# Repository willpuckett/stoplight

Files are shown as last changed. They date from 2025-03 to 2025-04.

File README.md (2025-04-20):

# 🚥 Stoplight

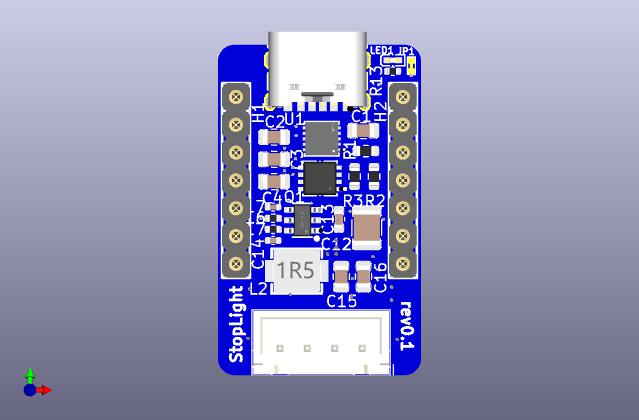
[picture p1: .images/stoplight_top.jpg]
top_view


### Features

- TMC2209 Stepper Driver
- 1 Ω Sense Resistors (tuned for small motors)
- HUSB238 PD Controller for dynamic Voltage Control
- On-board temperature sensing

Stoplight is a Xiao shield for operating small stepper motors. It is designed
specifically for 28-BYJ48, although it _may_ work with other small (0.225 RMS Amps or less) steppers as
well. It aims to provide utility all around the home, and is especially useful
when working with blinds and knobs.

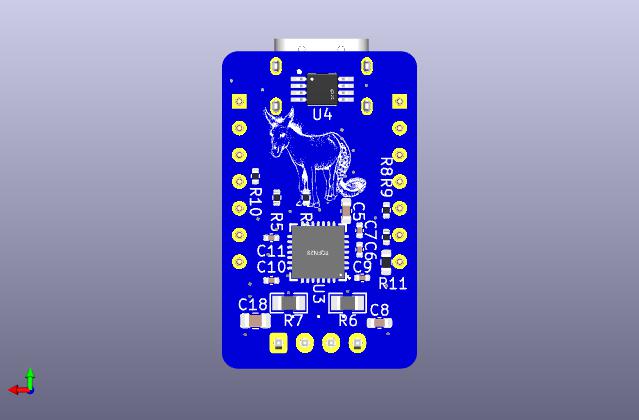
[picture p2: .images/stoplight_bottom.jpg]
rear pcb view


Commercial stepsticks have sense resistors that are not properly sized for
'smaller' motors to take advantage of TMC2209's features, including
stallguard.

> StopLight brings stall sensing to commodity/low cost, high torque motors.

Stoplight seeks to remedy these issues, while also providing software selectable
voltage control and temperature measurement in a package that works well with
HomeAssistant/ESPHome.

### Todo 

- [ ] TVS Protection
- [ ] Change C14 to same as C18 (BOM Consolidation)
- [ ] Consider removing DIAG and just using UART events instead
- [ ] Consider reconneacting fan port
- [ ] Address DS18B20U reading high 
- [ ] Test fit in mini blind housing
- [ ] Dim LED brightness
- [x] Test StallGuard tuning
  - ✅ works very well at 12v+
  - ⚠️ 9v is untested 
  - 🚦 5v is more finicky
- [x] Add esphome sample yaml's

## Homing

homing demo

## Fabrication

Use the [production files](jlcpcb/production_files/) to upload to jlc. Or first run [available here](https://octule.com/listing/1891073906/stoplight).

You'll need to swap the motor wires to a JST XH 4 pin housing. In addition to
removing the red cable, you also **must** perform the
[bipolar mod](https://ardufocus.com/howto/28byj-48-bipolar-hw-mod/) on your
steppers.

## Example HomeAssistant Config

The build sometimes fails, but can usually be completed by repeatedly pressing
'Retry', or switching to 'arduino' framework.

### Tuning

<details><summary>This demo exposes a number of controls to make tuning StallGuard easier.</summary>

```yaml
substitutions:
  name: "stoplight"
  friendly_name: "StopLight"
  board: "seeed_xiao_esp32c3"

# board/wifi/ota stuff
packages:
  device_base: !include .esp32.yaml

esp32:
  framework:
    type: esp-idf

logger:
  level: DEBUG

esphome:
  on_boot:
    - tmc2209.configure:
        direction: cw # or ccw
        microsteps: 1
        interpolation: True
        enable_spreadcycle: False
        tcool_threshold: 0
        tpwm_threshold: 0
    - tmc2209.stallguard:
        threshold: 23
    - tmc2209.currents:
        standstill_mode: freewheeling
        run_current: 0.150 # was 0.240
        hold_current: 0
    - button.press: home # home right after boot

external_components:
  - source: github://slimcdk/esphome-custom-components
    components: [tmc2209_hub, tmc2209, stepper]
  - source: github://pr#6693
    components: [husb238]

globals:
  - id: has_homed
    type: bool
    initial_value: "true"
    restore_value: no
  - id: homing_speed
    type: int
    initial_value: "480"
    restore_value: True

web_server:
  port: 80

i2c:
  sda: GPIO6
  scl: GPIO7
  frequency: 800kHz

uart:
  tx_pin: GPIO21
  rx_pin: GPIO20
  baud_rate: 500000 # 9600 -> 500k

one_wire:
  - platform: gpio
    pin: GPIO10

stepper:
  - platform: tmc2209
    id: driver
    # https://www.klipper3d.org/TMC_Drivers.html#limitations
    max_speed: 2000 steps/s # was 4000
    acceleration: 1000 steps/s^2 # was 2500
    deceleration: 1000 steps/s^2 # was 2500
    index_pin: GPIO3
    diag_pin: GPIO4
    rsense: 1000 mOhm
    config_dump_include_registers: False
    vsense: False
    analog_current_scale: False
    on_stall:
      - logger.log: "Motor stalled!"
      - if:
          condition:
            lambda: return !id(has_homed);
          then:
            - stepper.stop: driver
            - tmc2209.configure:
                direction: cw # or ccw
                microsteps: 1
                interpolation: True
                enable_spreadcycle: False
                tcool_threshold: 0
            - stepper.report_position:
                id: driver
                position: 0
            - globals.set:
                id: has_homed
                value: "true"
            - logger.log: "Home position set"
            - tmc2209.disable
    on_status:
      - logger.log:
          format: "Driver is reporting an update! (code %d)"
          args: ["code"]
      - if:
          condition:
            lambda: return code == tmc2209::DIAG_TRIGGERED;
          then:
            - logger.log: DIAG_TRIGGERED
      - if:
          condition:
            lambda: return code == tmc2209::DIAG_TRIGGER_CLEARED;
          then:
            - logger.log: DIAG_TRIGGER_CLEARED
      - if:
          condition:
            lambda: return code == tmc2209::RESET;
          then:
            - logger.log: RESET
      - if:
          condition:
            lambda: return code == tmc2209::RESET_CLEARED;
          then:
            - logger.log: RESET_CLEARED
      - if:
          condition:
            lambda: return code == tmc2209::DRIVER_ERROR;
          then:
            - logger.log: DRIVER_ERROR
      - if:
          condition:
            lambda: return code == tmc2209::DRIVER_ERROR_CLEARED;
          then:
            - logger.log: DRIVER_ERROR_CLEARED
      - if:
          condition:
            lambda: return code == tmc2209::CP_UNDERVOLTAGE;
          then:
            - logger.log: CP_UNDERVOLTAGE
      - if:
          condition:
            lambda: return code == tmc2209::CP_UNDERVOLTAGE_CLEARED;
          then:
            - logger.log: CP_UNDERVOLTAGE_CLEARED
      - if:
          condition:
            lambda: return code == tmc2209::OVERTEMPERATURE_PREWARNING;
          then:
            - logger.log: OVERTEMPERATURE_PREWARNING
      - if:
          condition:
            lambda: return code == tmc2209::OVERTEMPERATURE_PREWARNING_CLEARED;
          then:
            - logger.log: OVERTEMPERATURE_PREWARNING_CLEARED
      - if:
          condition:
            lambda: return code == tmc2209::OVERTEMPERATURE;
          then:
            - logger.log: OVERTEMPERATURE
      - if:
          condition:
            lambda: return code == tmc2209::OVERTEMPERATURE_CLEARED;
          then:
            - logger.log: OVERTEMPERATURE_CLEARED
      - if:
          condition:
            lambda: return code == tmc2209::TEMPERATURE_ABOVE_120C;
          then:
            - logger.log: TEMPERATURE_ABOVE_120C
      - if:
          condition:
            lambda: return code == tmc2209::TEMPERATURE_BELOW_120C;
          then:
            - logger.log: TEMPERATURE_BELOW_120C
      - if:
          condition:
            lambda: return code == tmc2209::TEMPERATURE_ABOVE_143C;
          then:
            - logger.log: TEMPERATURE_ABOVE_143C
      - if:
          condition:
            lambda: return code == tmc2209::TEMPERATURE_BELOW_143C;
          then:
            - logger.log: TEMPERATURE_BELOW_143C
      - if:
          condition:
            lambda: return code == tmc2209::TEMPERATURE_ABOVE_150C;
          then:
            - logger.log: TEMPERATURE_ABOVE_150C
      - if:
          condition:
            lambda: return code == tmc2209::TEMPERATURE_BELOW_150C;
          then:
            - logger.log: TEMPERATURE_BELOW_150C
      - if:
          condition:
            lambda: return code == tmc2209::TEMPERATURE_ABOVE_157C;
          then:
            - logger.log: TEMPERATURE_ABOVE_157C
      - if:
          condition:
            lambda: return code == tmc2209::TEMPERATURE_BELOW_157C;
          then:
            - logger.log: TEMPERATURE_BELOW_157C
      - if:
          condition:
            lambda: return code == tmc2209::OPEN_LOAD;
          then:
            - logger.log: OPEN_LOAD
      - if:
          condition:
            lambda: return code == tmc2209::OPEN_LOAD_CLEARED;
          then:
            - logger.log: OPEN_LOAD_CLEARED
      - if:
          condition:
            lambda: return code == tmc2209::OPEN_LOAD_A;
          then:
            - logger.log: OPEN_LOAD_A
      - if:
          condition:
            lambda: return code == tmc2209::OPEN_LOAD_A_CLEARED;
          then:
            - logger.log: OPEN_LOAD_A_CLEARED
      - if:
          condition:
            lambda: return code == tmc2209::OPEN_LOAD_B;
          then:
            - logger.log: OPEN_LOAD_B
      - if:
          condition:
            lambda: return code == tmc2209::OPEN_LOAD_B_CLEARED;
          then:
            - logger.log: OPEN_LOAD_B_CLEARED
      - if:
          condition:
            lambda: return code == tmc2209::LOW_SIDE_SHORT;
          then:
            - logger.log: LOW_SIDE_SHORT
      - if:
          condition:
            lambda: return code == tmc2209::LOW_SIDE_SHORT_CLEARED;
          then:
            - logger.log: LOW_SIDE_SHORT_CLEARED
      - if:
          condition:
            lambda: return code == tmc2209::LOW_SIDE_SHORT_A;
          then:
            - logger.log: LOW_SIDE_SHORT_A
      - if:
          condition:
            lambda: return code == tmc2209::LOW_SIDE_SHORT_A_CLEARED;
          then:
            - logger.log: LOW_SIDE_SHORT_A_CLEARED
      - if:
          condition:
            lambda: return code == tmc2209::LOW_SIDE_SHORT_B;
          then:
            - logger.log: LOW_SIDE_SHORT_B
      - if:
          condition:
            lambda: return code == tmc2209::LOW_SIDE_SHORT_B_CLEARED;
          then:
            - logger.log: LOW_SIDE_SHORT_B_CLEARED
      - if:
          condition:
            lambda: return code == tmc2209::GROUND_SHORT;
          then:
            - logger.log: GROUND_SHORT
      - if:
          condition:
            lambda: return code == tmc2209::GROUND_SHORT_CLEARED;
          then:
            - logger.log: GROUND_SHORT_CLEARED
      - if:
          condition:
            lambda: return code == tmc2209::GROUND_SHORT_A;
          then:
            - logger.log: GROUND_SHORT_A
      - if:
          condition:
            lambda: return code == tmc2209::GROUND_SHORT_A_CLEARED;
          then:
            - logger.log: GROUND_SHORT_A_CLEARED
      - if:
          condition:
            lambda: return code == tmc2209::GROUND_SHORT_B;
          then:
            - logger.log: GROUND_SHORT_B
      - if:
          condition:
            lambda: return code == tmc2209::GROUND_SHORT_B_CLEARED;
          then:
            - logger.log: GROUND_SHORT_B_CLEARED

button:
  - platform: template
    name: Home
    id: home
    on_press:
      - logger.log: "Going home!"
      - tmc2209.configure:
          direction: cw # or ccw
          microsteps: 1
          interpolation: True
          enable_spreadcycle: False
          tcool_threshold: 104
          tpwm_threshold: 0
      # - lambda: id(driver)->write_register(TPWMTHRS, 0);
      # - lambda: id(driver)->write_register(TCOOLTHRS, 1048575);
      - globals.set:
          id: has_homed
          value: "false"
      - stepper.set_speed:
          id: driver
          # 60 to 300 rpm
          speed: !lambda return id(homing_speed);
      - stepper.set_target:
          id: driver
          target: -9999999
  - platform: template
    name: Stop
    id: stop
    on_press:
      - logger.log: "Stopping!"
      - stepper.stop: driver
      - tmc2209.disable
  - platform: template
    name: 1000 Steps forward
    on_press:
      - logger.log: "Going forward!"
      - stepper.set_speed:
          id: driver
          speed: 400 steps/s
      - stepper.set_target:
          id: driver
          target: !lambda return id(driver)->current_position +1000;
      # - tmc2209.disable

husb238:
  id: husb_01

binary_sensor:
  - platform: husb238
    attached: "PD Attached"

  - platform: template
    name: "Has Homed"
    lambda: return id(has_homed);

text_sensor:
  - platform: husb238
    status: "Last request status"
    capabilities: "Capabilities"

select:
  - platform: husb238
    voltage: "Voltage selector"

sensor:
  - platform: husb238
    voltage: "Contracted Voltage"
    current: "Contracted Current"
    selected_voltage: "Selected Voltage"

  - platform: dallas_temp
    name: temperature

  - platform: tmc2209
    type: stallguard_result
    name: Driver stallguard
    update_interval: 10s

  - platform: tmc2209
    type: actual_current
    name: Actual current
    update_interval: 10s

  - platform: tmc2209
    type: motor_load
    name: Motor load
    update_interval: 10s

  # - platform: tmc2209
  #   type: pwm_scale_sum
  #   name: PWM Scale Sum
  #   update_interval: 250ms

  # - platform: tmc2209
  #   type: pwm_scale_auto
  #   name: PWM Scale Auto
  #   update_interval: 250ms

  # - platform: tmc2209
  #   type: pwm_ofs_auto
  #   name: PWM OFS Auto
  #   update_interval: 250ms

  # - platform: tmc2209
  #   type: pwm_grad_auto
  #   name: PWM Grad Auto
  #   update_interval: 250ms

number:
  - platform: template
    name: Target position
    min_value: -999999
    max_value: 999999
    step: 100
    lambda: return id(driver)->current_position;
    update_interval: 10s
    set_action:
      - stepper.set_target:
          id: driver
          target: !lambda "return x;"

  - platform: template
    name: Homing RPM
    min_value: 0
    max_value: 300
    step: 1
    lambda: return id(homing_speed) * 60 / 32;
    update_interval: 10s
    set_action:
      - globals.set:
          id: homing_speed
          value: !lambda "return x * 32 / 60;"

  - platform: template
    name: SGTHRS
    min_value: 0
    max_value: 255
    step: 1
    lambda: return id(driver)->read_register(SGTHRS);
    update_interval: 10s
    set_action:
      - lambda: id(driver)->write_register(SGTHRS, x);

  - platform: template
    name: TCOOLTHRS
    min_value: 0
    max_value: 1048575
    step: 1
    lambda: return id(driver)->read_register(TCOOLTHRS);
    update_interval: 10s
    set_action:
      - lambda: id(driver)->write_register(TCOOLTHRS, x);

  - platform: template
    name: "Run Current"
    min_value: 0
    max_value: 31
    step: 1
    lambda: return id(driver)->read_field(IRUN_FIELD);
    update_interval: 10s
    set_action:
      - tmc2209.currents:
          irun: !lambda "return x;"
```
</details>

### Wall Heater

<details><summary>This demo implements a knob controlled wall heater.</summary>

```yaml
substitutions:
  name: "heater"
  friendly_name: "Wall Heater"
  board: "seeed_xiao_esp32c3"

# board/wifi/ota stuff
packages:
  device_base: !include .esp32.yaml

esphome:
  on_boot:
    # - lambda: id(husb_01)->command_request_voltage(5);
    - tmc2209.configure:
        direction: cw # or ccw
        microsteps: 1
        interpolation: True
        enable_spreadcycle: False
        tcool_threshold: 0
        tpwm_threshold: 0
    - tmc2209.stallguard:
        threshold: 23
    - tmc2209.currents:
        standstill_mode: freewheeling
        run_current: 0.1375 # was 0.150
        hold_current: 0
    - button.press: probe_low # home right after boot

external_components:
  - source: github://slimcdk/esphome-custom-components
    components: [ tmc2209_hub, tmc2209, stepper ]
  - source: github://pr#6693
    components: [ husb238 ]

globals:
  - id: steps
    type: int
    restore_value: yes
    initial_value: "1000"

i2c:
  sda: GPIO6
  scl: GPIO7 
  frequency: 800kHz

uart:
  tx_pin: GPIO21
  rx_pin: GPIO20
  baud_rate: 500000 # 9600 -> 500k

one_wire:
  - platform: gpio
    pin: GPIO10

husb238:
  id: husb_01

stepper:
  - platform: tmc2209
    id: driver
    max_speed: 480 steps/s
    acceleration: 1000 steps/s^2 
    deceleration: 1000 steps/s^2 
    index_pin: GPIO3
    diag_pin: GPIO4
    rsense: 1000 mOhm
    on_stall:
      - stepper.stop: driver
      - logger.log: Endstop Detected 🍍

script:
  - id: move_stepper
    mode: restart
    parameters:
      # use 0/false for low side endstop, 1/true for high side
      homing: bool
      target: int
    then:
      - lambda: id(husb_01)->command_request_voltage(20);
      - tmc2209.configure:
          tcool_threshold: !lambda 'return homing ? 104 : 0;'
      - stepper.set_speed:
          id: driver
          speed: 480 steps/s
      - delay: 1s
      - stepper.set_target:
          id: driver
          target: !lambda 'return target;'
      - wait_until:
          condition:
            lambda: 'return id(driver)->has_reached_target();'
      - logger.log:
          format: "Moved to %d steps"
          args: [ 'id(driver)->current_position' ]
      - tmc2209.disable:
          id: driver 
      - lambda: id(husb_01)->command_request_voltage(5);

button:
  - platform: template
    name: Probe Low
    id: probe_low 
    on_press:
      - climate.control:
          id: pid_climate
          mode: 'OFF'
      - script.execute: 
          id: move_stepper
          homing: true
          target: -9999999
      - script.wait: move_stepper
      - stepper.report_position:
          id: driver
          position: 0
      - logger.log:
          format: "Probed to %d steps"
          args: [ 'id(driver)->current_position' ]
      
  - platform: template
    name: Probe High
    id: probe_high
    on_press:
      - climate.control:
          id: pid_climate
          mode: 'OFF'
      - script.execute: 
          id: move_stepper
          homing: true
          target: 9999999
      - script.wait: move_stepper
      - globals.set:
          id: steps
          value: !lambda 'return id(driver)->current_position;'
 
  - platform: template
    name: "PID Climate Autotune"
    on_press:
      - climate.pid.autotune: pid_climate

sensor:
  - platform: husb238
    voltage: "Contracted Voltage"

  - platform: template
    name: "Steps"
    id: steps_display
    icon: "mdi:shoe-print"
    accuracy_decimals: 0
    lambda: 'return id(steps);'

  - platform: dallas_temp
    id: ds_temp
    filters: 
      - lambda: return x - 13.5;

  # This sensor takes the output from the pid heater and transforms it to step numbers
  - platform: pid
    name: "PID Climate Heat"
    id: heat_float
    type: HEAT
    filters:
      - round_to_multiple_of: 10
      - delta: 9
    on_value:
      then:
        - script.execute: 
            id: move_stepper
            homing: false
            target: !lambda 'return static_cast<int>(id(steps) * (x / 100));'

# This is just a fake output to make the pid heater happy.
# Ideally, the pin will use the onboard led, but I'm not sure what the pin number is for that...
output:
  - platform: ledc
    pin: GPIO2
    id: heater_output

# Example configuration entry
climate:
  - platform: pid
    name: "PID Climate Controller"
    id: pid_climate
    sensor: ds_temp
    default_target_temperature: 21°C
    heat_output: heater_output
    control_parameters:
      kp: 4
      ki: 0.4
      kd: 0.5
      output_averaging_samples: 5      # smooth the output over 5 samples
      derivative_averaging_samples: 5  # smooth the derivative value over 5 samples
    # deadband_parameters:
    #   threshold_high: 0.5°C
    #   threshold_low: -1.0°C
    #   kp_multiplier: 0.5   # proportional gain reduced inside deadband
    #   ki_multiplier: 0.25   # integral accumulates at only 25% of normal ki
    #   kd_multiplier: 0.5   # derviative is reduced inside deadband
    #   deadband_output_averaging_samples: 5   # average the output over 15 samples within the deadband
```

</details>

### Blinds

<details><summary>StallGuard blinds operation</summary>

```yaml
substitutions:
  name: "blins03"
  blind_number: right
  friendly_name: "Right Blind"
  board: "seeed_xiao_esp32c3"
  delay: "1s"

# board/wifi/ota stuff
packages:
  device_base: !include .esp32.yaml

esphome:
  on_boot:
    - tmc2209.configure:
        direction: ccw # or ccw
        microsteps: 1
        interpolation: True
        enable_spreadcycle: False
        tcool_threshold: 0
        tpwm_threshold: 0
    - tmc2209.stallguard:
        threshold: 45 
    - tmc2209.currents:
        standstill_mode: freewheeling
        run_current: 0.1375 # was 0.150
        hold_current: 0

external_components:
  - source: github://slimcdk/esphome-custom-components
    components: [ tmc2209_hub, tmc2209, stepper ]
  - source: github://pr#6693
    components: [ husb238 ]

globals:
  - id: steps
    type: int
    restore_value: yes
    initial_value: "1000"

i2c:
  sda: GPIO6
  scl: GPIO7 
  frequency: 800kHz

uart:
  tx_pin: GPIO21
  rx_pin: GPIO20
  baud_rate: 500000 # 9600 -> 500k

one_wire:
  - platform: gpio
    pin: GPIO10

husb238:
  id: husb_01

stepper:
  - platform: tmc2209
    id: driver
    max_speed: 480 steps/s
    acceleration: 1000 steps/s^2 
    deceleration: 1000 steps/s^2 
    index_pin: GPIO3
    diag_pin: GPIO4
    rsense: 1000 mOhm
    on_stall:
      - stepper.stop: driver
      - logger.log: Endstop Detected 🍍

script:
  - id: move_stepper
    mode: restart
    parameters:
      # use 0/false for low side endstop, 1/true for high side
      homing: bool
      target: int
    then:
      - lambda: id(husb_01)->command_request_voltage(12);
      - tmc2209.configure:
          tcool_threshold: !lambda 'return homing ? 104 : 0;'
      - stepper.set_speed:
          id: driver
          speed: !lambda 'return homing ? 480 : 120;'
      - delay: 1s
      - stepper.set_target:
          id: driver
          target: !lambda 'return target;'
      - while:
          condition:
            lambda: 'return !id(driver)->has_reached_target();'
          then:
            - cover.template.publish:
                id: ${name}_${blind_number}
                position: !lambda 'return float( id(driver).current_position ) / float( id(steps) );' 
                current_operation: !lambda 'return id(driver).current_position < id(driver).target_position ? COVER_OPERATION_OPENING : COVER_OPERATION_CLOSING;'
            - delay: ${delay}
      - logger.log:
          format: "Moved to %d steps"
          args: [ 'id(driver)->current_position' ]
      - tmc2209.disable:
          id: driver 
      - lambda: id(husb_01)->command_request_voltage(5);
      - cover.template.publish:
          id: ${name}_${blind_number}
          position: !lambda 'return float( id(driver).current_position ) / float( id(steps) );' 
          current_operation: IDLE

button:
  - platform: template
    name: Probe Low
    id: probe_low 
    on_press:
      - script.execute: 
          id: move_stepper
          homing: true
          target: -9999999
      - script.wait: move_stepper
      - stepper.report_position:
          id: driver
          position: 0
      - logger.log:
          format: "Probed to %d steps"
          args: [ 'id(driver)->current_position' ]
      
  - platform: template
    name: Probe High
    id: probe_high
    on_press:
      - script.execute: 
          id: move_stepper
          homing: true
          target: 9999999
      - script.wait: move_stepper
      - globals.set:
          id: steps
          value: !lambda 'return id(driver)->current_position;'

sensor:
  - platform: husb238
    voltage: "Contracted Voltage"

  - platform: template
    name: "Steps"
    id: steps_display
    icon: "mdi:shoe-print"
    accuracy_decimals: 0
    lambda: 'return id(steps);'

  - platform: dallas_temp
    id: ds_temp
    filters: 
      - lambda: return x - 13.5;

cover:
  - platform: template
    name: "${blind_number}"
    id: ${name}_${blind_number}
    open_action:
      then:
        - logger.log: "Opening"
        - button.press: probe_high
    close_action:
      then:
        - logger.log: "Closing"
        - button.press: probe_low
    position_action:
      then:
        - logger.log: "Jostling"
        - script.execute: 
            id: move_stepper
            homing: false
            target: !lambda return int(id(steps) * pos);
    stop_action:
      then:
        - script.execute: 
            id: move_stepper
            homing: false
            target: !lambda return id(driver).current_position;
    has_position: true
    device_class: blind

switch:
  - platform: template
    name: "Reset ${blind_number}"
    id: reset_${name}_${blind_number}
    turn_on_action:
      - button.press: probe_low
      - script.wait: move_stepper
      - button.press: probe_high
      - script.wait: move_stepper
      - button.press: probe_low
      - script.wait: move_stepper
      - switch.turn_off: reset_${name}_${blind_number}
```

</details>

## Schematic

schematic

## Reference

[TMC2209 Calaulations Worksheet](https://www.analog.com/media/en/engineering-tools/design-tools/TMC2209_Calculations.xlsx)

[BTT-TMC2209-v1.2](https://pax.deno.dev/bigtreetech/BIGTREETECH-TMC2209-V1.2@master/Schematic/TMC2209-V1.2.pdf?b)

[Cookie Robotics](https://cookierobotics.com/042/)

[jangeox](http://www.jangeox.be/2013/10/change-unipolar-28byj-48-to-bipolar.html)

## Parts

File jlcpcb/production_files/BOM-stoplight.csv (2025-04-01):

Comment | Designator | Footprint | LCSC | Quantity
4K7 | R12 | R_0402_1005Metric | C105871 | 1
56pF | C8 | C_0402_1005Metric | C107007 | 1
10R | R1 | R_0603_1608Metric | C109318 | 1
2K2 | R10,R11 | R_0402_1005Metric | C114762 | 2
22K1@1% | R4 | R_0402_1005Metric | C163478 | 1
TPS54202DDCR | U1 | SOT-23-6_L2.9-W1.6-P0.95-LS2.8-BL | C191884 | 1
TMC2209-LA-T | U3 | QFN-28_L5.0-W5.0-P0.50-BL-EP | C2150710 | 1
1uF/50V | C3 | C_0805_2012Metric | C215803 | 1
1K | R13 | R_0603_1608Metric | C22548 | 1
5K1 | R3 | R_0603_1608Metric | C23186 | 1
Conn_01x04_Socket | J1 | JST_XH_B4B-XH-A_1x04_P2.50mm_Vertical | C23398778 | 1
MDA4020-100M | L1 | IND-SMD_L4.5-W4.1_YXMAA0402 | C2847473 | 1
MF254V-11-07-0743 | H1,H2 | HDR-TH_7P-P2.54-V-F_MF254V-11-07-0743 | C2889988 | 2
12R | R14 | R_0402_1005Metric | C2909317 | 1
10uF/25v | C1 | C_1210_3225Metric | C2918502 | 1
49.9K | R2 | R_0603_1608Metric | C2930109 | 1
4.7uF | C5,C6,C9 | C_0805_2012Metric | C2991173 | 3
0.1uF/25v | C2 | C_0603_1608Metric | C3011652 | 1
1R00 | R8,R9 | R0805 | C346776 | 2
DOZ30P03 | Q1 | PDFN-8_L3.1-W3.0-P0.65-LS3.3-BL | C36499166 | 1
100K@1% | R5 | R_0402_1005Metric | C60491 | 1
22uF | C10,C18,C7 | C_0805_2012Metric | C6119901 | 3
TYPE-C 6P(073) | USB1 | TYPE-C-SMD_TYPE-C-6P_5 | C668623 | 1
DS18B20U | U4 | MSOP-8_L3.0-W3.0-P0.65-LS4.9-BL | C695836 | 1
HUSB238_002DD | U2 | DFN-10_L3.0-W3.0-P0.50-BL-EP2.5 | C7471904 | 1
100nF/50V | C12,C15,C16,C17,C4 | C_0402_1005Metric | C77020 | 5
22nF/50V | C11 | C_0402_1005Metric | C77023 | 1
1uF/50V | C14 | C_0603_1608Metric | C90540 | 1
4.7uF | C13 | C_0603_1608Metric | C913474 | 1
20K | R6,R7 | R_0402_1005Metric | C93942 | 2
XL-1005UGC | LED1 | LED0402-RD_GREEN | C965793 | 1

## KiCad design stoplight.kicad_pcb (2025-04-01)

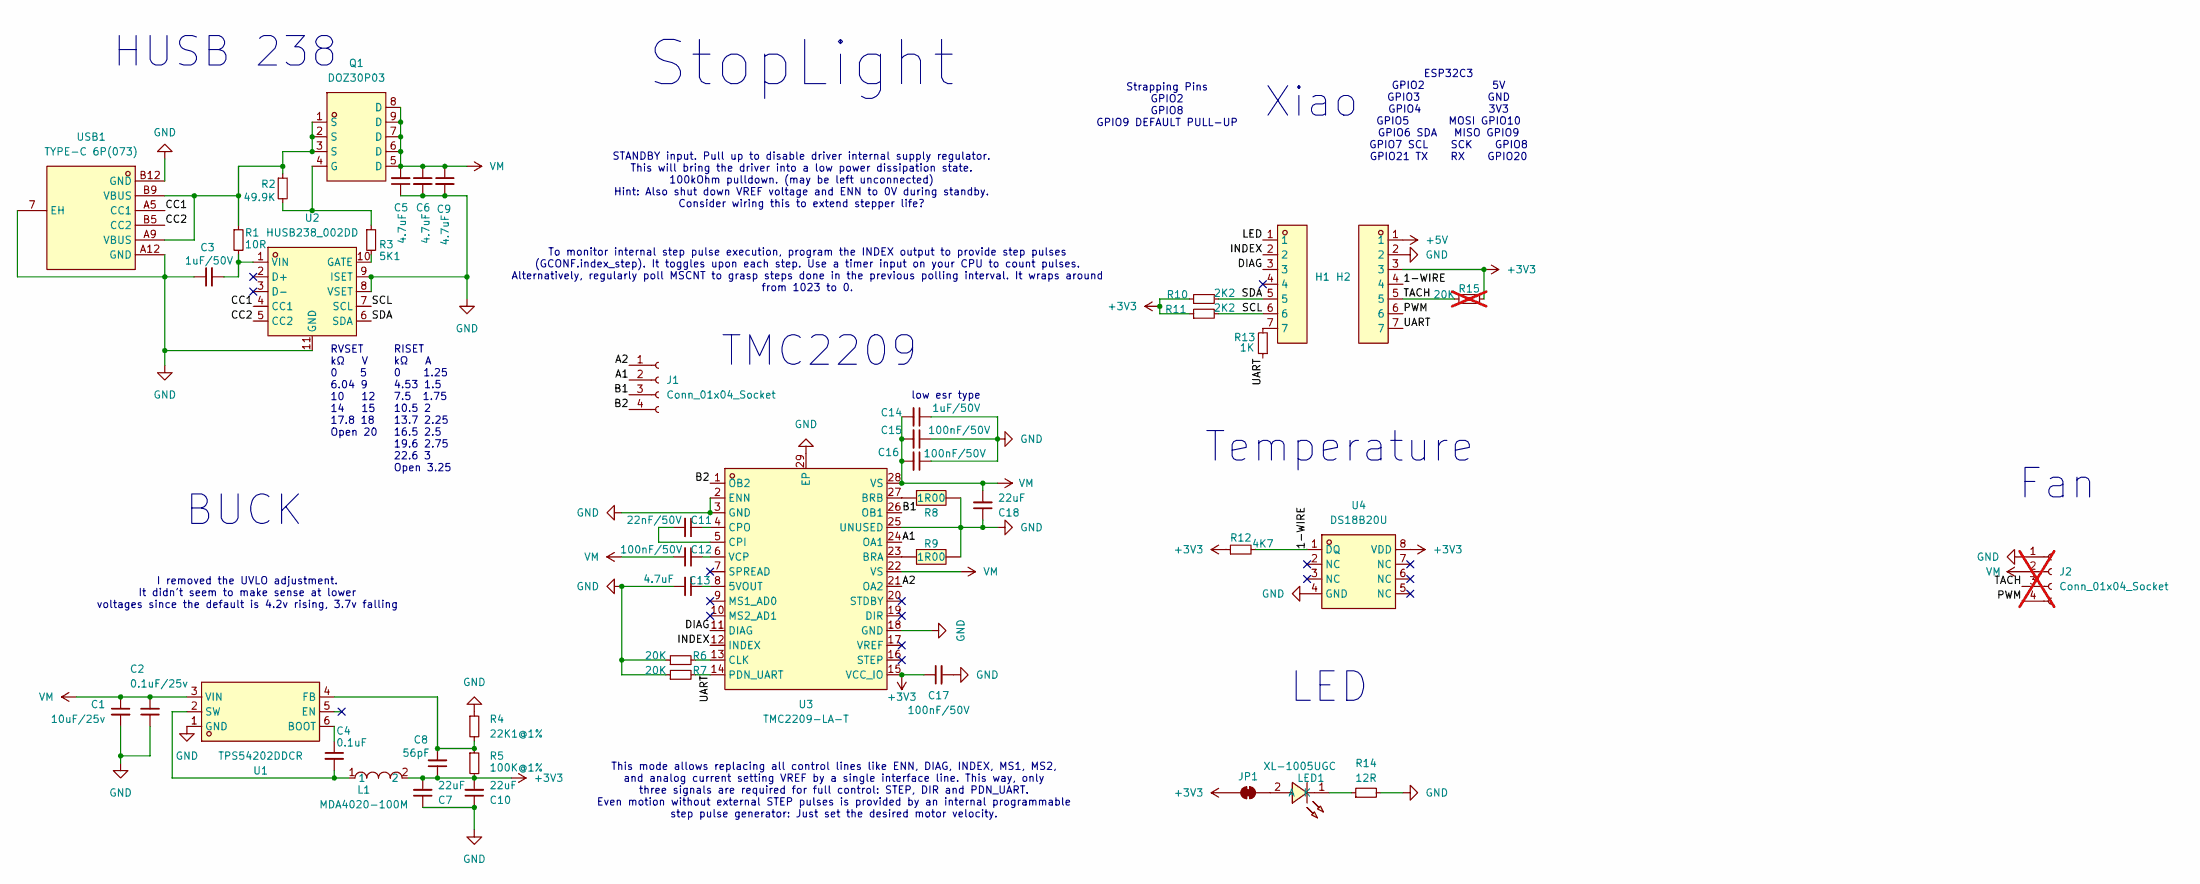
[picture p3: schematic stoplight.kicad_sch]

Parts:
C1: 10uF/25v; C_1210_3225Metric; LCSC C2918502
C2: 0.1uF/25v; C_0603_1608Metric; LCSC C3011652
C3: 1uF/50V; C_0805_2012Metric; LCSC C215803
C4: 0.1uF; C_0402_1005Metric; LCSC C77020
C5, C6, C9: 4.7uF; C_0805_2012Metric; LCSC C2991173
C7, C10, C18: 22uF; C_0805_2012Metric; LCSC Part C6119901
C8: 56pF; C_0402_1005Metric; LCSC C107007
C11: 22nF/50V; C_0402_1005Metric; LCSC C77023
C12, C15, C16, C17: 100nF/50V; C_0402_1005Metric; LCSC C77020
C13: 4.7uF; C_0603_1608Metric; LCSC C913474
C14: 1uF/50V; C_0603_1608Metric; LCSC C90540
H1, H2: MF254V-11-07-0743; HDR-TH_7P-P2.54-V-F_MF254V-11-07-0743; LCSC Part C2889988
J1: Conn_01x04_Socket; JST_XH_B4B-XH-A_1x04_P2.50mm_Vertical; LCSC C23398778
J2: Conn_01x04_Socket; FanPinHeader_1x04_P2.54mm_Vertical; not fitted
JP1: SolderJumper_2_Bridged; Solder_Jumper_Tight
L1: MDA4020-100M; IND-SMD_L4.5-W4.1_YXMAA0402; LCSC Part C2847473
LED1: XL-1005UGC; LED0402-RD_GREEN; LCSC Part C965793
Q1: DOZ30P03; PDFN-8_L3.1-W3.0-P0.65-LS3.3-BL; LCSC Part C36499166
R1: 10R; R_0603_1608Metric; LCSC C109318
R2: 49.9K; R_0603_1608Metric; LCSC C2930109
R3: 5K1; R_0603_1608Metric; LCSC C23186
R4: 22K1@1%; R_0402_1005Metric; LCSC C163478
R5: 100K@1%; R_0402_1005Metric; LCSC C60491
R6, R7: 20K; R_0402_1005Metric; LCSC C93942
R8, R9: 1R00; R0805; LCSC Part C346776
R10, R11: 2K2; R_0402_1005Metric; LCSC C114762
R12: 4K7; R_0402_1005Metric; LCSC C105871
R13: 1K; R_0603_1608Metric; LCSC C22548
R14: 12R; R_0402_1005Metric; LCSC Part C2909317
R15: 20K; R_0402_1005Metric; not fitted
U1: TPS54202DDCR; SOT-23-6_L2.9-W1.6-P0.95-LS2.8-BL; LCSC Part C191884
U2: HUSB238_002DD; DFN-10_L3.0-W3.0-P0.50-BL-EP2.5; LCSC Part C7471904
U3: TMC2209-LA-T; QFN-28_L5.0-W5.0-P0.50-BL-EP; LCSC Part C2150710
U4: DS18B20U; MSOP-8_L3.0-W3.0-P0.65-LS4.9-BL; LCSC Part C695836
USB1: TYPE-C 6P(073); TYPE-C-SMD_TYPE-C-6P_5; LCSC Part C668623

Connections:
+3V3: C7.2, C8.1, C10.2, C17.1, H2.3, JP1.1 (A), L1.2, R5.2, R10.1, R11.1, R12.1, R15.2, U3.15 (VCC_IO), U4.8 (VDD)
+5V: H2.1
/1-WIRE: H2.4, R12.2, U4.1 (DQ)
/A1: J1.2, U3.24 (OA1)
/A2: J1.1, U3.21 (OA2)
/B1: J1.3, U3.26 (OB1)
/B2: J1.4, U3.1 (OB2)
/CC1: U2.4 (CC1), USB1.A5 (CC1)
/CC2: U2.5 (CC2), USB1.B5 (CC2)
/DIAG: H1.3, U3.11 (DIAG)
/INDEX: H1.2, U3.12 (INDEX)
/LED: H1.1
/PWM: H2.6, J2.4
/SCL: H1.6, R11.2, U2.7 (SCL)
/SDA: H1.5, R10.2, U2.6 (SDA)
/TACH: H2.5, J2.3, R15.1
/UART: H2.7, R7.2, R13.1, U3.14 (PDN_UART)
GND: C1.2, C2.1, C3.1, C5.1, C6.2, C7.1, C9.2, C10.1, C13.2, C14.1, C15.1, C16.1, C17.2, C18.1, H2.2, J2.1, R4.1, R6.1, R7.1, R8.2, R9.2, R14.2, U1.1 (GND), U2.8 (VSET), U2.9 (ISET), U2.11 (GND), U3.2 (ENN), U3.3 (GND), U3.18 (GND), U3.25 (UNUSED), U3.29 (EP), U4.4 (GND), USB1.7 (EH), USB1.A12 (GND), USB1.B12 (GND)
unnamed: H1.7, R13.2
unnamed: JP1.2 (B), LED1.2 (A)
unnamed: LED1.1 (K), R14.1
unnamed: Q1.4 (G), R2.2, R3.1
unnamed: Q1.1 (S), Q1.2 (S), Q1.3 (S), R1.1, R2.1, USB1.A9 (VBUS), USB1.B9 (VBUS)
unnamed: C4.1, U1.6 (BOOT)
unnamed: C8.2, R4.2, R5.1, U1.4 (FB)
unnamed: C4.2, L1.1, U1.2 (SW)
unnamed: R3.2, U2.10 (GATE)
unnamed: C3.2, R1.2, U2.1 (VIN)
unnamed: C13.1, U3.8 (5VOUT)
unnamed: R9.1, U3.23 (BRA)
unnamed: R8.1, U3.27 (BRB)
unnamed: R6.2, U3.13 (CLK)
unnamed: C11.2, U3.5 (CPI)
unnamed: C11.1, U3.4 (CPO)
unnamed: C12.1, U3.6 (VCP)
VM: C1.1, C2.2, C5.2, C6.1, C9.1, C12.2, C14.2, C15.2, C16.2, C18.2, J2.2, Q1.5 (D), Q1.6 (D), Q1.7 (D), Q1.8 (D), Q1.9 (D), U1.3 (VIN), U3.22 (VS), U3.28 (VS)

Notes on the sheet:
Strapping Pins GPIO2 GPIO8 GPIO9 DEFAULT PULL-UP
Xiao
TMC2209
I removed the UVLO adjustment. It didn't seem to make sense at lower voltages since the default is 4.2v rising, 3.7v falling
STANDBY input. Pull up to disable driver internal supply regulator. This will bring the driver into a low power dissipation state. 100kOhm pulldown. (may be left unconnected) Hint: Also shut down VREF voltage and ENN to 0V during standby. Consider wiring this to extend stepper life?
low esr type
To monitor internal step pulse execution, program the INDEX output to provide step pulses (GCONF.index_step). It toggles upon each step. Use a timer input on your CPU to count pulses. Alternatively, regularly poll MSCNT to grasp steps done in the previous polling interval. It wraps around from 1023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
RVSET kΩ V 0 5 6.04 9 10 12 14 15 17.8 18 Open 20
StopLight
LED
Fan
RISET kΩ A 0 1.25 4.53 1.5 7.5 1.75 10.5 2 13.7 2.25 16.5 2.5 19.6 2.75 22.6 3 Open 3.25
This mode allows replacing all control lines like ENN, DIAG, INDEX, MS1, MS2, and analog current setting VREF by a single interface line. This way, only three signals are required for full control: STEP, DIR and PDN_UART. Even motion without external STEP pulses is provided by an internal programma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
Temperature
HUSB 238
BUCK
ESP32C3 GPIO2 5V GPIO3 GND GPIO4 3V3 GPIO5 MOSI GPIO10 GPIO6 SDA MISO GPIO9 GPIO7 SCL SCK GPIO8 GPIO21 TX RX GPIO20

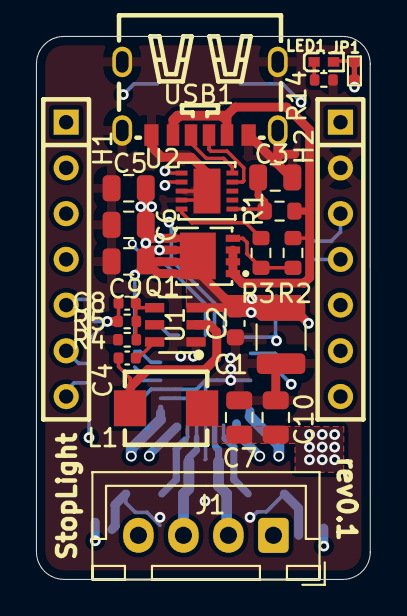
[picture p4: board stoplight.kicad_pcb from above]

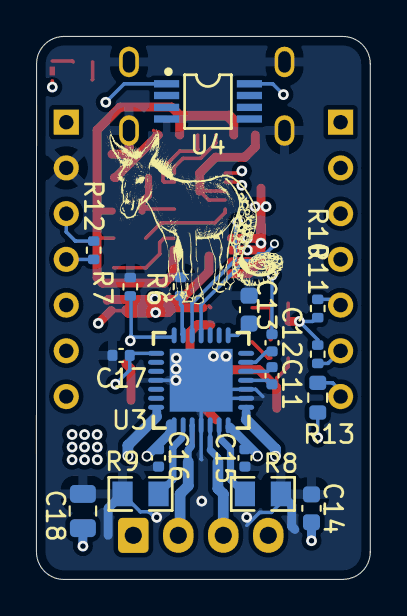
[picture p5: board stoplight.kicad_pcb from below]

Board: 4 copper layers, 18.5 x 30.2 mm, 44 parts (18 on the bottom side), 32 nets.

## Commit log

2025-03-31 change to stoplight
    [BOM-pepper_stepper.csv, BOM-stoplight.csv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]
2025-04-01 add power pours and additional vias
    [BOM-stoplight.csv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]
2025-04-16 Add Solderpad Hardware License v2.1
2025-04-18 add heater example to readme
